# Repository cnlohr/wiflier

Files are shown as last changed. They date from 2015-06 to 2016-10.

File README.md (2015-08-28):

# wiflier, An ESP8266-based Quadcopter Brain

WARNING: This project is still in its early stages!  It doesn't fly yet!

WARNING: Everything surrounding a control loop in control.c for flight IS SUPER JANKEY AND TOTALLY NOT HOW IT SHOULD BE!

WARNING: When I operated the PWM at 3kHz, I had to modify my current board to add pullups on the I2C and short out the AVR's reset to VBat, otherwise it seemed to reboot randomly during flight.

Do you think quadcopters are neat?  Eh, not really for me... BUT I THINK ESP8266's ARE AWESOME!  So, I slapped an LSM9DS1 IMU, a BMP085 barometer and an AVR co-processor with 4 PWM output drivers to a PCB small enough to fit in a hubsan X4 quadcopter.

Picture of the wiflier brain

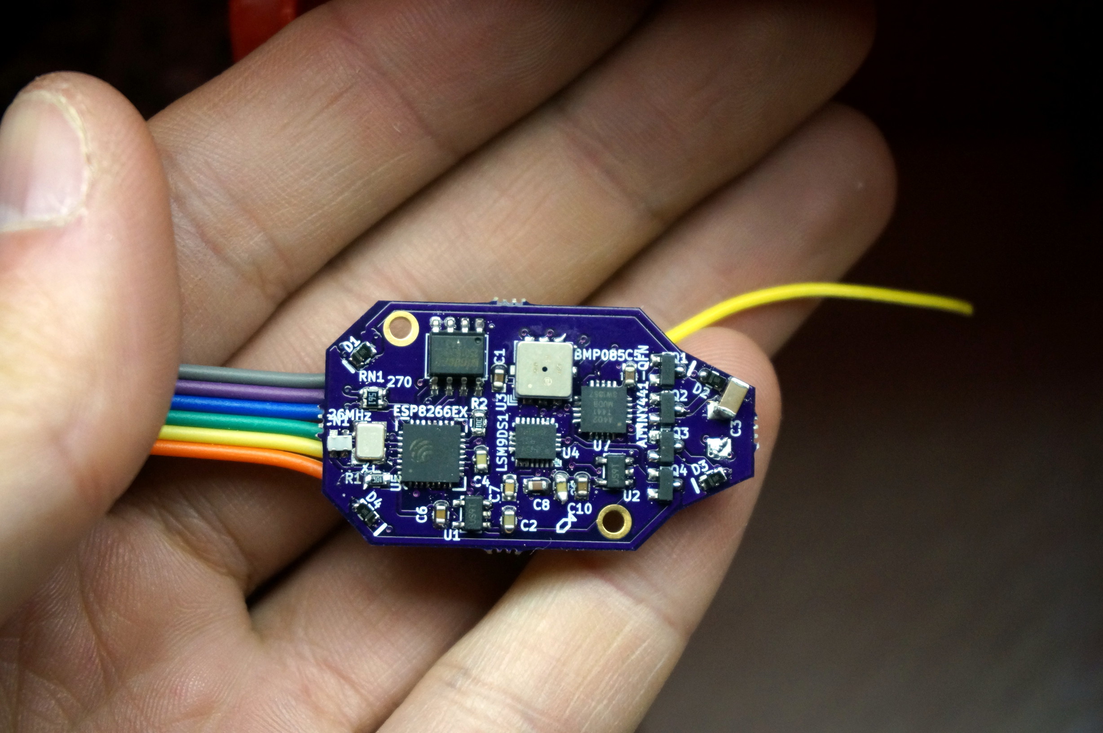
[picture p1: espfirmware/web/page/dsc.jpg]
Picture of Device


Youtube video of the first crack at this:

[!(http://img.youtube.com/vi/3n76iMTHXuE/0.jpg)](http://www.youtube.com/watch?v=3n76iMTHXuE) 

## The Hardware

There is an ESP8266, a 32-bit 80(or 160)MHz processor with 802.11bgn networking at the heart of the system.  This run all the user interface code, and handles all control algorithms.  It is attached to a 2 MByte flash for code and data storage.  It is connected via a software i2c bus to:

* An ATTiny441 with 4 PWM outputs and battery voltage monitoring.
   * 4 6-amp N-channel fets, with diode proection on the AVR's output channels to drive DC motors.
   * Safe-mode, which ramps PWM down after periods of inactivity.
* A LSM9DS1, 9-axis IMU with temperature sensor.  It has a gyro, accelerometer, and magnetometer built in.
* A BMP085, barometer with high precision temperature sensor built in.

## Network connectivity

The wiflier uses an ESP8266, which can act as either a station (mode 1) or a softap (mode 2).  Softap means it broadcasts a SSID that other compuers can connect to.

### Station (Mode 1)

Station mode can be initialized by the ```W1:[ssid]:password``` command.  This will cause the wiflier to connect to the specified network.  It supports WEP, WPA-PSK, and WPA2-PSK.  It will remember this setting when it boots up.  If it fails to connect, it will revert to mode 2.  Currently (maybe?) if it reverts to mode 2, it will stay in mode 2 every subsequent bootup.

If it succeeds in negotiating, it will pull a DHCP lease and print to the serial terminal what that DHCP release is.  All communicat

### Soft AP (Mode 2)

Soft AP mode allows the ESP8266 to create its own wifi network that you can connect to with a wifi-enabled device.  In this mode, one can connect to the new network, and visit the ESP at 192.168.4.1.

This is the default mode.

## Command Interfaces

There are currently two command interfaces to the wiflier.  One is UDP, on port 7777, the other is via HTTP at http://[ip]/d/issue?.

### The UDP interface

For the UDP interface, you can use netcat or 'nc' to communicate with the ESP.  This is partciularly convenient as a command-line tool. You can type

```
nc [ip] 7777 -u
```

To open a terminal to the wiflier.  You can type `T1` and enter.  This should provide a constant stream of telemetry.

When using the UDP interface, you must only have one command per packet.  Packets are the delineation of commands.

### The HTTP interface

If you make an HTTP request to `http://[ip]/d/issue?[command]` where [ip] is the address of the wiflier, and [command] is the command you are issuing, the command will be executed and its return value is sent.  You can check this interface's functionality by going to `http://192.168.4.1/d/issue?T0` and verify it returns a T0 confirmation.  Anything after the question mark will be urldecoded.  Things like amphersands should be URL encoded.

### The websockets interface.

This interface does not yet exist, but I hope to make it a reality.

## Building

This code is separated into two pieces, the ESP firmware and the AVR firmware.

The ESP firmware requires the esp_iot_sdk_v1.1.0, and a copy of the ESP8266 GCC toolchain.  To build the ESP firmware, cd to the espfirmware folder and type 'make'.

The AVR firmware requires avr-libc-1.8.0 and avr-gcc-4.8.1 at a minimum.  To build the AVR firmware, cd to the avr folder, and type 'make'.

## Memory layout:

We use a bit of a modified take on the old memory layout since, while we support OTA upgrades, we do so in a different way than the normal way.

| Address | Size  | Name / Description |
| --- |:-----:| --- |
| 00000h  | 64k | 0x00000.bin, IRAM Code | 
| 10000h  | 180k  | Normally unused, HTTP may be here if signature found.  |
| 3C000h  | 4k | May be used by web interface  |
| 3D000h  | 4k | our device configuration |
| 3E000h  | 8k | May be used by ESP SDK. |
| 40000h  | 240k  | 0x40000.bin, Cached code. |
| 7C000h  | 8k | May be used by ESP SDK. |
| 7E000h  | 8k | May be WiFi configuration |
| 80000h  | 512k  | Scratchpad (Temp only!) |
| 100000h | 1M+ | HTTP data, 1M on W25Q16.  HTTP Used here if signature found. |

## Hardware designs

The wiflier schematics and PCB layout is done in KiCad (2013-07-03).  It should be compatible with newer versions, but is unlikely to be compatible with older versions.  In the hardware/ folder, you'll also find wiflier.lst.  This contains the part identifier, name, digikey part number (if applicable) and cost assuming an order of ~10 boards.

## wiflier UART

The UART on the wiflier is used to send debugging information.  The Wiflier does not currently accept commands via the UART.  I intend to make the UART available to GPS or video input.

## UART flashing the ESP8266.

To UART flash the ESP8266 you will need esptool.py and a serial TTL uart.  USB to serial converters are good. *Do not* use RS-232-level UARTs.  To flash this, you will need to:

1. De-power the device. 
2. Connect GPIO0 to GND.
3. Connect TX, RX and GND (And possibly power) to your UART, reversing TX/RX lines.
4. Apply power to the device.  
5. Then go to the espfirmware folder, and type:

    ```
    ~/esp8266/esptool/esptool.py --port /dev/ttyUSB0 write_flash 0x00000 0x00000.bin 0x40000 0x40000.bin
    ```
    
    or

    ```
    make burn
    ```

6. The esptool should reboot into the running code.

## Net flashing the ESP8266.

Net Flashing the ESP8266 is particularly easy.  Connect to the wiflier, verify you can communicate to it (via HTTP or ping).  Use the 'execute_reflash' tool with the following commands:

```
web/execute_reflash 192.168.4.1 0x00000.bin 0x40000.bin
```

or, from the espfirmware folder...

```
make netburn
```

This will connect to 192.168.4.1, and it will perform the following steps:

1. It will attempt to erase the blocks that need to be written (to 0x00000.bin) using the "FB" command.
  * And await confirmation.
2. It will write the data (0x00000.bin) using the "FW" command.
  * And await confirmation.
3. It will write this first file to 80000h, then it will repeat for the second file, to c0000h.
4. It will then compute the MD5 of the files and execute the "FM" command.
5. Internally, the wiflier will verify the integrety of the written files.
6. At this point, it will disable all interrupts.  Network will go down, etc.
7. It will copy the data from 80000h to 00000h, and then copy c0000h to 40000h.
8. It will then reboot itself and boot into the new code.
9. If a network wasn't found, and it switches to being its own AP... next boot, it should still try to join the old network.

## Flashing the AVR

The AVR is particularly easy to flash.  You'll need:

  * An ISP Programmer, like the TinyISP that operates a 3.3V outputs.
    * Under *NO* condition use a programmer that haves 5V outputs.  This will almost certainly cause severe damage to the wiflier.
  * Associated 6-pin ISP programming connector.
  * AVRDude, or other ISP programming software.
  * A 6-pin male-male connector, SMD preferred.

To flash, follow the following steps:

  1. Connect to a wiflier command interface.
  2. Use the "B0" command to make the ESP8266 release the bus.
    * Failure to do this may damage the AVR or ESP.
  3. Plug the 6-pin male connector into the programming header on the programmer.
  4. Hold the 6-pin connector on the back of the PCB. 
    * Reversing the order will not program, but will not damage the part.
    * You can determine proper order by unplugging power to the quadcopter and flipping the connector around until it powers on.  Powering on indicates proper order.
  5. Initiate programming of the AVR.
	* Failures may indicate the ESP is locking the bus lines.
    * Failures may indicate not all the pins are making contact.
    * Failures may indicate the programming header is reversed.
    * Failures may indicate other problems in the toolchain, i.e. not running programmer as root or having proper credentials.
  6. Remove programmer.
  7. Use the "B1" command to bring the ESP8266 Back online.

## TODO

### Software modifications:

* Try one-shotting the sensors (currently they're in free-run) this will synchronize them to the system clock.
* Try making the system switch over to calling the control loop on interrupt after connection is negotiated, rather than using flags and the idle loop.
* Add WebSockets?
* Add WebGL?
* Separate the control.c into different parts.
* Have some minimal levels of protection for writing to flash, i.e. maybe only allow writing to 0x80000+
* Send some sort of broadcast or discovery packets.
* Figure out why the AVR needs soooo many bytes before it accepts data.

### Hardware modifications:

* Consider making the sensors slaves to the AVR, and having the ESP communicate only to the AVR.
* Consider using the MPL3115A2 instead of the BMP085
* I keep looking at the lack of pullups on the I2C and it makes me nervous when we're running the motor controllers.

## Commands

The heart of the wiflier is the command engine.  This command engine is human-readable, and with the exception of some use cases of the flashing commands is human-readable.

Commands are very simple, they are basically single letters, then parameters, separated by colons.  Responses are usually similar to the command that was sent.  A failure can be indicated by either a lack of response, or an exclaimation point (!) prefixing the response.

As a warning, in some places \r\n is used and in others \n is used.  You should discard \r in all non-binary uses.

### Bn (B1 / B0):  Turn main control loop on/off
Turning the main control loop off will stop all I2C bus communication and resolving what to do in the control loop.  That also means telemetry will stop.

### D
Reboot the system.  This includes the bootloader.  If GPIO0 is held low, the serial bootloader will be initiated.

### Tn (T1 / T0):  Turn streaming of calibrated, filtered telemetry data on/off
This will either continously stream, or turn off streaming of the calibrated telemetry data from the sensors.  Calibration is done using the Rn and Z commands.  Data is tab deliniated.

The streaming format is: ```TD: [frame #]  [GyroX]  [GyroY]  [GyroZ]  [AccX]  [AccY]  [AccZ]  [MagX]  [MagY]  [MagZ]  [Pressure in Bar]  [Temperature in tenths of degrees C]  [battery voltage in 1/100ths of a volt]\n```

### Un (U1 / U0):  Turn streaming of uncalibrated/raw telemtry data on/off
This will enable/disable streaming of uncalibrated telemetry data, straight from the sensors.   Data is tab deliniated.

The streaming format is: ```UD: [frame #]  [GyroX]  [GyroY]  [GyroZ]  [AccX]  [AccY]  [AccZ]  [MagX]  [MagY]  [MagZ]  [Pressure in Bar]  [Temperature in tenths of degrees C]  [battery voltage in 1/100ths of a volt]\n```

For example:
```
UD   9224      600      199      137     2839     1790     2080       61     2214    -4673    101233    368    499 \r\n
UD   9225     -616     -244      304     3208     1797     1934       40     2229    -4673    101233    368    507 \r\n
UD   9226     -687     -234      318     3374     1815     1893       74     2259    -4683    101233    368    507 \r\n
UD   9227      242      240       43     2960     1795     2051       31     2223    -4691    101233    368    507 \r\n
UD   9228      455      146       46     3122     1708     1964       37     2226    -4664    101237    368    507 \r\n
```

### Z: Set 'zero'
Sending a Z will set the zero all gyros, and accelerometer X and accelerometer Y.  This will only have an effect on the calibrated, filtered telemetry data.

### Rn (R1 / R0): Enable range calibration.
When you want to begin range calibration (for accelerometer Z, and all mag inputs) send R1.  This will begin to look for peak positive and negative values.  When you execute R0, it will take whatever the maximums are and scale all data to that range.

### P: Print calibration and other system data.
When you send a 'P' command, the wiflier will send back all calibration and possibly other system data.  As of the time of writing this the following values are returned:

```
    P6
    #GC\t x \t y \t z (Gyro Zero)
    #AC\t x \t y \t z (Accelerometer Zero)
    #AL\t x \t y \t z (Accelerometer Minimum)
    #AM\t x \t y \t z (Accelerometer Maximum)
    #ML\t x \t y \t z (Magnetometer Minimum)
    #MH\t x \t y \t z (Magnetometer Maximum)
```

### S: Save calibration and other settings.
This writes the current information in the global `settings` value to the flash at address 3D000h.

### Mx: Motor control functions

#### M?: Motor query

Returns if motors are in automatic mode (1/0) and all motor speeds, 0..255 speed.

`M?` will return `M?[automatic]:[M0 speed]:[M1 speed]:[M2 speed]:[M3 speed]\r\n"

#### MA: Motors in automatic mode

Selecting this function will move the move the motors into automatic mode, allowing a control algorithm to take them over.

(Not currently implemented)

#### MM: Motors in manual mode

Disable automatic control of motors, they will now respond to the M(number) commands.  Optionally, can take up to 4 arguments for the new motor set values.

#### M0, M1, M2, M3: Set motor speed.

If you want to control an individual motor speed, you call `Mn:speed` for example `M0:127` would turn motor 0 on to half duty cycle.  This only works if the motors are in manual mode.

### Fx: Flash commands

#### FEn: Flash Erase Sector

Erase a specific flash sector, it will erase the flash starting at address n*4096 to n*4096+4095.  This function works with flash memory below and above the 1MB barrier, however it takes a moment to execute and no interrupts may run while it is executing.

#### FBn: Flash Erase Block

Erase a specific block of flash.  This operates on a whole 64kB block, and takes about as long as it takes FE to erase just one sector.  This function does not work past the 1MB barrier.

#### FW: Flash Write

This function writes flash. It requires two parameters, the first is the starting addres, the second is the size (in bytes).   Writes must be aligned to 4-byte boundaries, sizes must line to 4-byte boundaries.

```
    FW40:8:hello\r\n
```

Will write `hello\r\n\0` to memory address 40 (which will break booting, so don't do this), and it will respond with:

```
    FW40
```

#### FR: Flash Read

This will read back from the flash, starting at the first parameter and with length of the second.

```
    FR40:8\r\n
```

Will read from address 40 8 bytes and if we've executed the terrible terrible example above, respond with:

```
    FR00000040:0008:hello\r\n\0
```

#### FM: Rewrite boot flash

This function takes several parameters, in the style: ```FMa:b:c:d:e:f:g:h``` where 

   1. A = Address to copy from #1
   2. B = Address to copy to #1  (Must be 65kB aligned)
   3. C = Number of bytes to copy #1 (Must be 1k chunks)
   4. D = MD5 of entire 'from #1' range.
   5. E = Address to copy from #2
   6. F = Address to copy to #2  (Must be 65kB aligned)
   7. G = Number of bytes to copy #2 (Must be 1k chunks)
   8. H = MD5 of entire 'from #2' range.

This will verify both MD5's before copying.  Interrupts will continue to execute until the actual flash-over begins.  Once flash-over is complete, the device will automatically reboot.

An example would be:

```
FM524288:0:33792:d6f04e459bc9aefabd9ed80981e6837f:786432:262144:171008:8435d1904110eacb66771320f63736bc
```

It should respond with ```FM``` In the event of a failure, it will also send a ```!FM[code]```.

### Wx: Wireless/Network commands.

#### W1: Connect to wifi network.

If you want to connect to an existing wifi network, you can use the W1 command.  This will find the specified AP, and join.  An example W1 command would be ```W1:ssid:password```.  This will connect to network with name 'ssid', and password 'password'.  If it fails to connect, it will switch back to softap mode.

#### W2: Make softAP network

This will cause the ESP8266 to make its own network. You can connect to it.  Its IP will be 192.168.4.1

#### WI: Get current settings

This will cause the ESP8266 to give you the mode (1 or 2) SSID, and password of the current network status.

For example ```WI``` will return ```WI1:mynetwork:mypassword```.

#### WS: Scan for networks

**WARNING**: If operating in mode 2, this will cause the ESP to go offline momentarily while it scans!

If you issue the ```WS``` command, the ESP8266 will begin a scan. It is unlikely to return any response at all. You can read the returned networks with the ```WR``` command.

It may take several seconds for the WS command to complete.

#### WR: Return wireless networks from last scan.

After you scan for networks, you can probe for responses to those networks with the ```WR``` command.  It returns ```WRn``` where n is the number of networks found.  It will then provide the networks in a tab delinated data format as follows:

```
#SSID MAC RSSI Channel Encryption
```

For example a response to the ```WR``` command could be:

```
WR3
#quiddles       00:23:15:11:22:41       -44     1       open
#reads          08:18:a0:02:4d:cc       -55     1       wpa2
#rguest         0a:14:c1:f3:02:a0       -68     11      open
```

### J: Joystick commands

***SECTION NOT WRITTEN***

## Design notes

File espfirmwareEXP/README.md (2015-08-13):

#ESP8266 I2S WS2812 Driver 

(For more reliable WS2812 driving...)

This project is based off of the I2S interface for the mp3 player found here:
https://github.com/espressif/esp8266_mp3_decoder/

If you want more information about the build environment, etc.  You should 
check out the regular WS2812 driver, found here: https://github.com/cnlohr/ws2812esp8266

This project is still jankey and needs some cleanup.  The way it currently works is to
continuously send WS2812 frames and when new data comes in on port 7777, it just updates the frames.

I wanted to make it so it would stop doing all DMA proesses so it could save bus contention, but I couldn't figure out how to make that happen.  If I tried disabling and re-enabling, it seems to have caused the DMA to just freak out and turn off until chip reboot.

The WS2812 output is synthesized from the input buffer.   Any time a 0 is to be transmitted, we need a .3us pulse high and .9us low.  If a 1, then we send a .9us high with a .3us low.  The way we do this is we look at nibbles, i.e.:

0101 would convert into:
1000 1110 1000 1110 < bitstream that actually gets shipped out.

Unfortunately this does mean it takes up 4x the space in RAM to DMA the data... But, it is very fast and efficient.

## Hardware Connection

Unfortunately the I2S Output pin is the same as RX1 (pin 25), which means if you are programming via the UART, it'll need to be unplugged any time you're testing.  The positive side of this is that it is a pin that is exposed on most ESP8266 breakout boards.

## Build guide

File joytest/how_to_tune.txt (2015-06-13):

THIS DOES NOT WORK!!!

To tune L/R: Set tuning to:
N0:0:0:12600:####:0:0:12600:0:0:0:12600

#### = High P value (400 worked for me)

Try running the craft.

Get an oscillation.

Open oscillation in OpenOffice.

Find period of oscillation (from 0 to high, to 0 to low to 0)

I.e. rows 2659 to 2724... 65

Zeigler Nichols says: Ku = 120, Tu = 65
 Kp = .6Ku     Kp = 72
 Ki = 2Kp/Tu   Ki = 3
 Kd = Kp*Tu/8  Kd = 585

N0:0:0:12600:72:3:585:12600:0:0:0:12600
Err try this:
NP1000:100:0:12600:16000:200:0:12600:16000:200:0:12600

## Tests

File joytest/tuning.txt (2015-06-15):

NP0:100:0:12600:2000:50:0:12600:2000:50:0:12600

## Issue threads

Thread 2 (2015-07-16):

How have you made the PCB?

Pablotis, 2015-07-16:
I suppose you have designed the PCB but, have you soldered it or have ordered it? Because it seems to be made from a machine, could you give me the link please?
A lot of thanks!!
I love your proyect!!

cnlohr, 2015-07-16:
Well, I used oshpark for the board and populated it myself.  BUT! I will be branching off in the next 2 weeks to a brand new version.  I can give you links to the old one if you want, BUT! The new one is coming soon, and once I'm sure I'm happy with the hardware, I might be getting them made professionally.

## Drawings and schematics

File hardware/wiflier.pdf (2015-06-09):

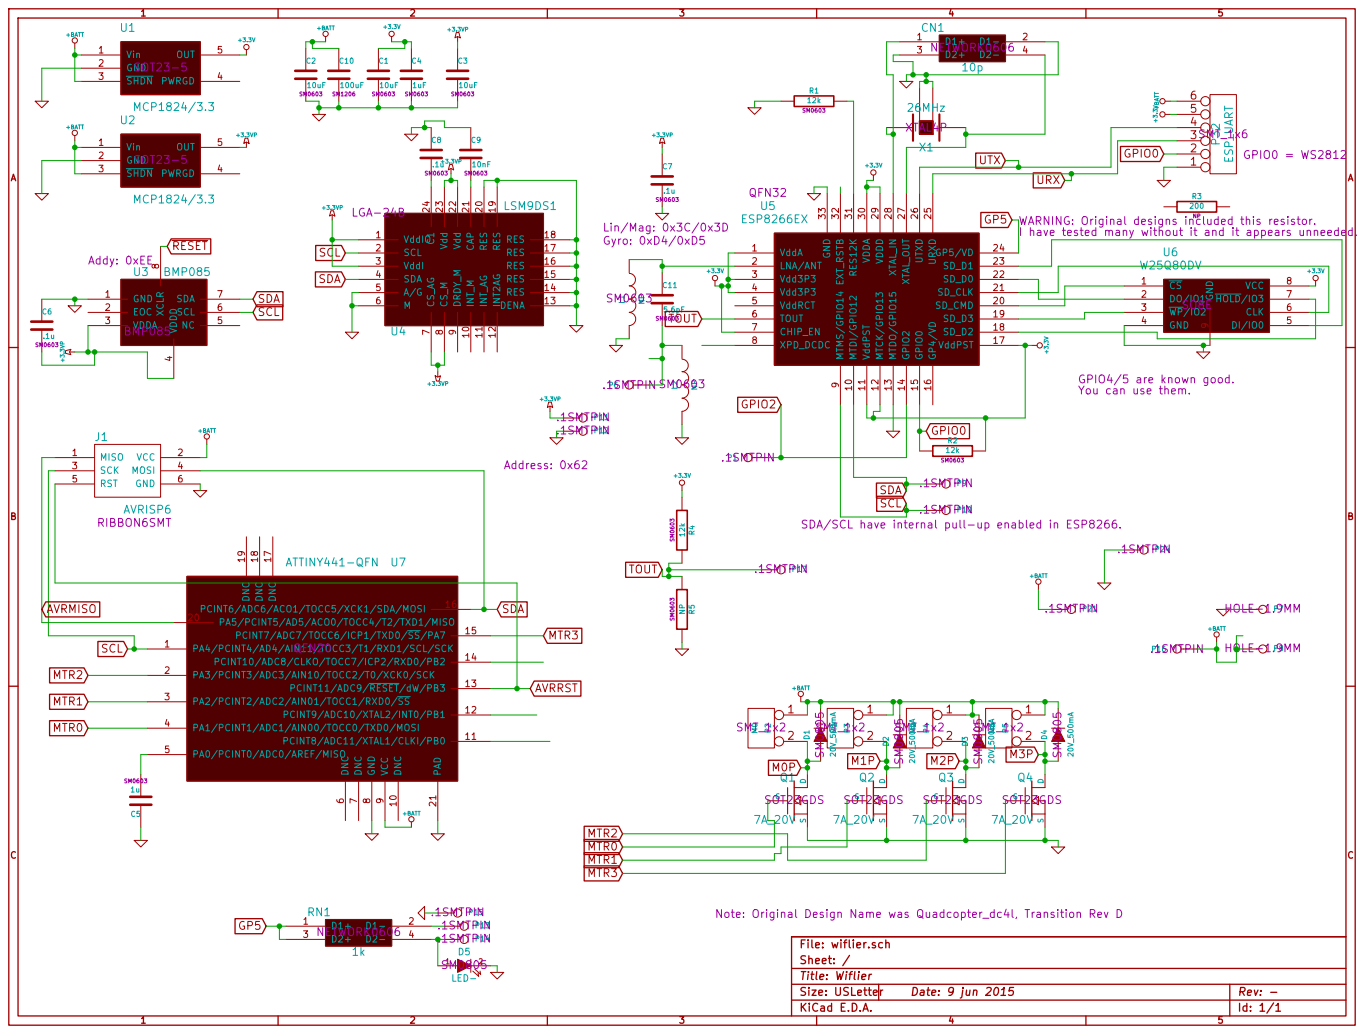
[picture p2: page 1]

I have tested many without it and it appears unneeded. R1

9 INT_M 10 RES 20 INT_AG 11 CAP 21 INT2AG 12 Vdd 22 DENA 13 Vdd 23 RES 14 C1 24 RES 15 RES 16 RES 17 RES 18 RES 19 U4

9 MTDI/GPIO12 10 SD_CMD 20 VDDA 30 VddPST 11 SD_CLK 21 RES12K 31 MTCK/GPIO13 12 SD_D0 22 EXT_RSTB 32 MTDO/GPIO15 13 SD_D1 23 GND 33 GPIO2 14 GP5/VD 24 GPIO0 15 URXD 25 GP4/VD 16 UTXD 26 VddPST 17 XTAL_OUT 27 SD_D2 18 XTAL_IN 28 SD_D3 19 VDDD 29U5 ESP8266EX

4 NC 5 SCL 6 SDA 7 XCLR

9 DNC 10 PA5/PCINT5/AD5/ACO0/TOCC4/T2/TXD1/MISO 20 PCINT8/ADC11/XTAL1/CLKI/PB0 11 PAD 21 PCINT9/ADC10/XTAL2/INT0/PB1 12 PCINT11/ADC9/RESET/dW/PB3 13 PCINT10/ADC8/CLKO/TOCC7/ICP2/RXD0/PB2 14 PCINT7/ADC7/TOCC6/ICP1/TXD0/SS/PA7 15 PCINT6/ADC6/ACO1/TOCC5/XCK1/SDA/MOSI 16 DNC 17 DNC 18 DNC 19 ATTINY441-QFN U7 QFN20 MISO 1 VCC 2 SCK 3 MOSI 4 RST 5 GND 6 J1 AVRISP6

Note: Original Design Name was Quadcopter_dc4l, Transition Rev D

Id: 1/1 Title: Wiflier File: wiflier.sch Sheet: /

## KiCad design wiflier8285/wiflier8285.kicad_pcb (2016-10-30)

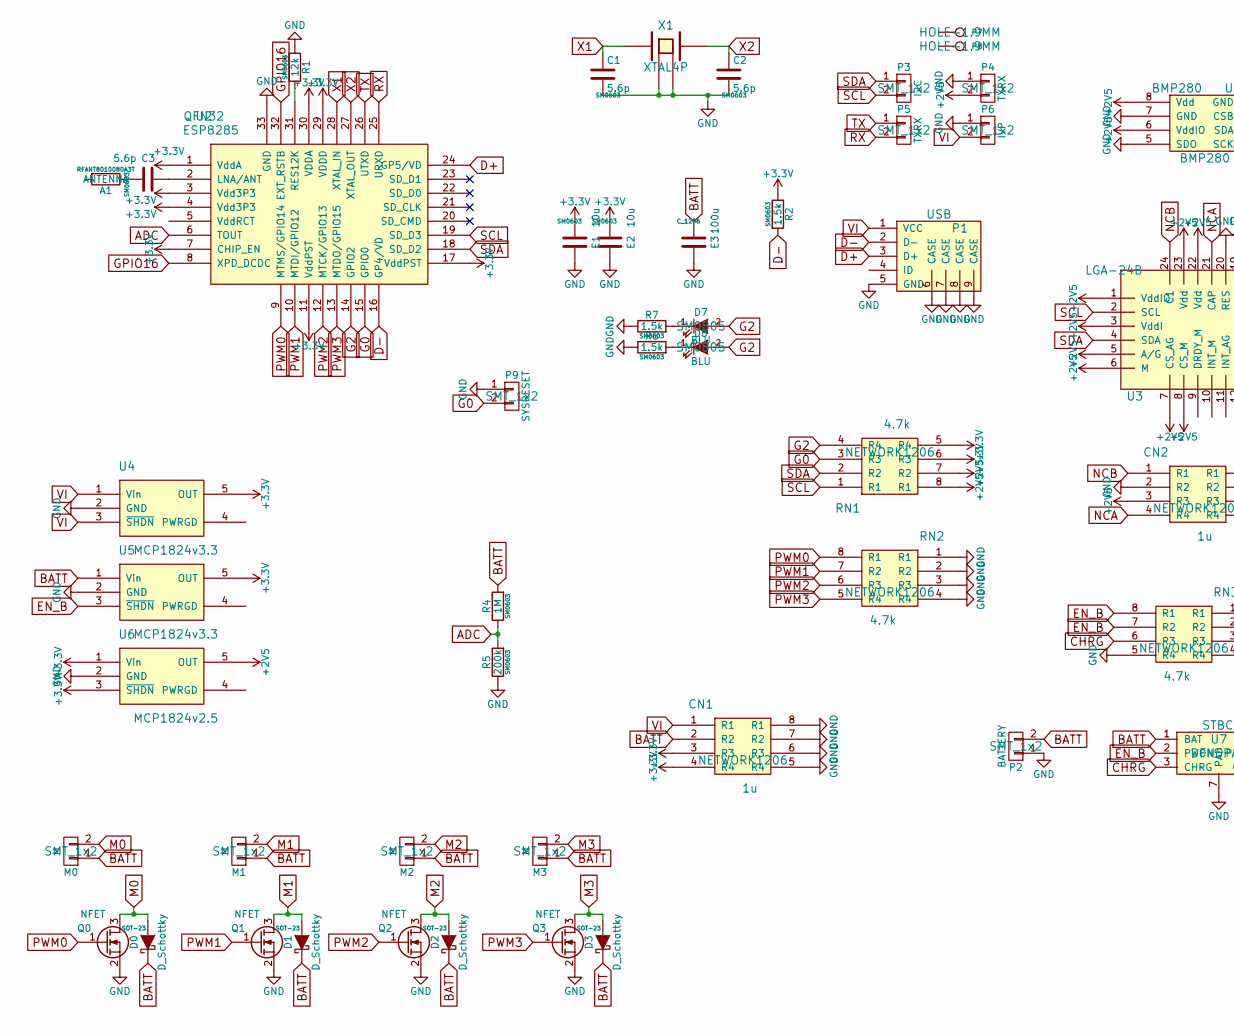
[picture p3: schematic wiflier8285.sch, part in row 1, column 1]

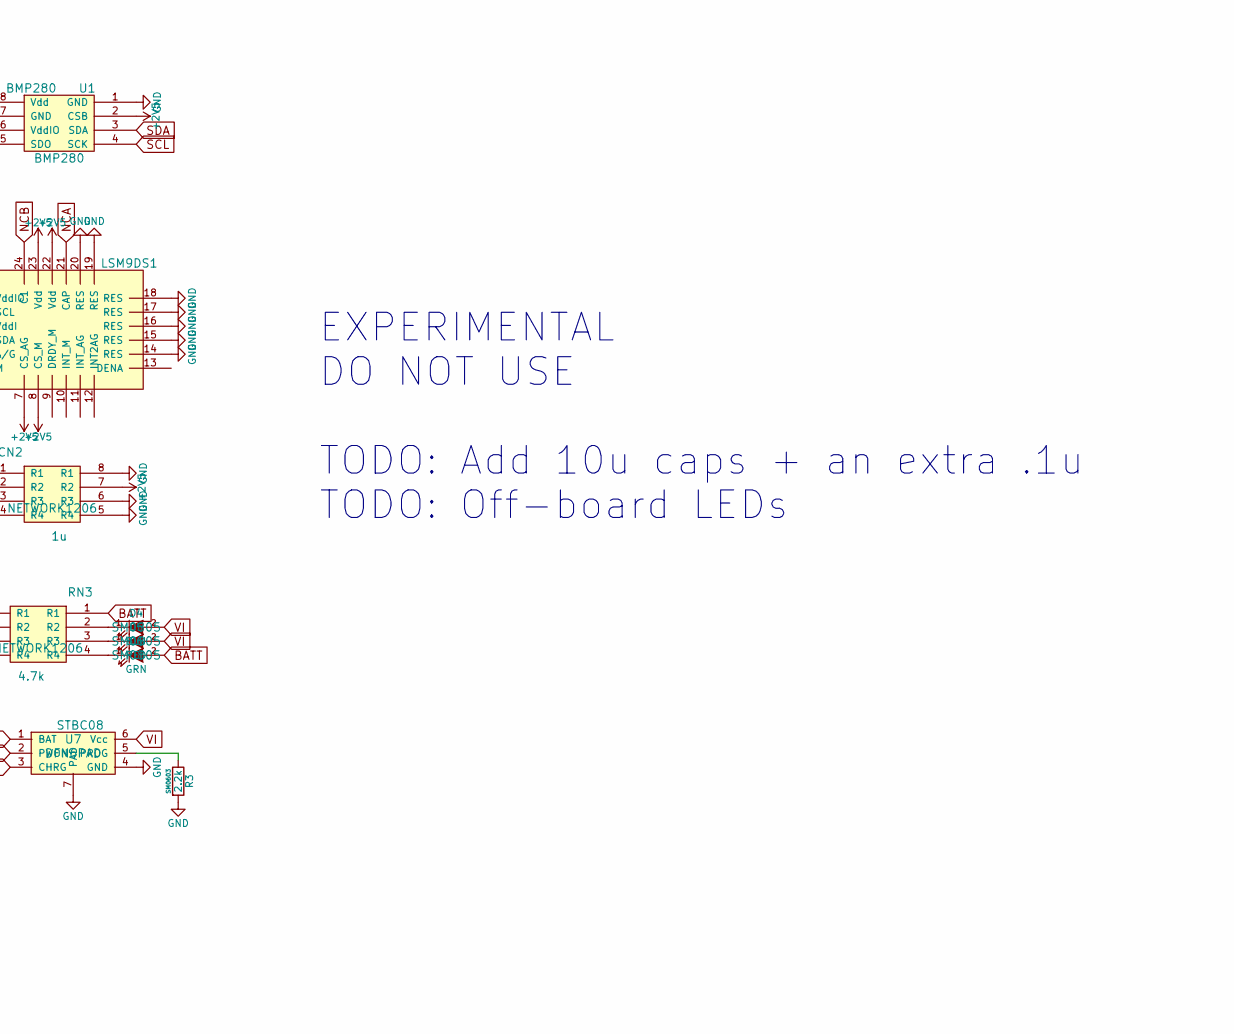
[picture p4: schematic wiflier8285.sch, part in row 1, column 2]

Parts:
A1: ANTENNA; RFANT8010080A3T
C1, C2, C3: 5.6p; SM0603
CN1, CN2: 1u; NETWORK1206
D0, D1, D2, D3: D_Schottky; SMini2-F5-B; Digikey DB2J41100LCT-ND
D4, D7, D8: BLU; SM0805
D5: RED; SM0805
D6: GRN; SM0805
E1, E2: 10u; SM0603
E3: 100u; C_1206
M0, M1, M2, M3: M; SMT_1x2
P1: USB; USBMicroB-10118194-0001LF
P2: BATTERY; SMT_1x2
P3: I2C; SMT_1x2
P4, P5: TXRX; SMT_1x2
P6: IVP; SMT_1x2
P7, P8: M; HOLE-1.9MM
P9: SYSRESET; SMT_1x2
Q0, Q1, Q2, Q3: NFET; SOT-23; Digikey IRLML6244TRPBFCT-ND
R1: 12k; SM0603
R2, R6, R7: 1.5k; SM0603
R3: 2.2k; SM0603
R4: 1M; SM0603
R5: 200k; SM0603
RN1, RN2, RN3: 4.7k; NETWORK1206
U1: BMP280
U2: ESP8285; QFN32
U3: LSM9DS1; LGA-24B
U4, U5: MCP1824v3.3; SOT-23-5
U6: MCP1824v2.5; SOT-23-5
U7: STBC08; DFN6PAD
X1: XTAL4P; XTAL4TINY

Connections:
+2V5: CN2.3 (R3), CN2.7 (R2), P4.2, RN1.7 (R2), RN1.8 (R1), U1.2 (CSB), U1.6 (VddIO), U1.8 (Vdd), U3.1 (VddIO), U3.3 (VddI), U3.5 (A/G), U3.6 (M), U3.7 (CS_AG), U3.8 (CS_M), U3.22 (Vdd), U3.23 (Vdd), U6.5 (OUT)
+3V3: CN1.3 (R3), CN1.4 (R4), E1.2, E2.2, R2.1, RN1.5 (R4), RN1.6 (R3), U2.1 (VddA), U2.3 (Vdd3P3), U2.4 (Vdd3P3), U2.7 (CHIP_EN), U2.11 (VddPST), U2.17 (VddPST), U2.29 (VDDD), U2.30 (VDDA), U4.5 (OUT), U5.5 (OUT), U6.1 (Vin), U6.3 (~SHDN)
ADC: R4.1, R5.2, U2.6 (TOUT)
BATT: CN1.2 (R2), D0.1 (K), D1.1 (K), D2.1 (K), D3.1 (K), D6.2 (A), E3.2, M0.1, M1.1, M2.1, M3.1, P2.2, R4.2, RN3.1 (R1), U5.1 (Vin), U7.1 (BAT)
CHRG: RN3.6 (R3), U7.3 (CHRG)
D+: P1.3 (D+), U2.24 (GP5/VD)
D-: P1.2 (D-), R2.2, U2.16 (GP4/VD)
EN_B: RN3.7 (R2), RN3.8 (R1), U5.3 (~SHDN), U7.2 (PWON)
G0: P9.2, RN1.3 (R3), U2.15 (GPIO0)
G2: D7.2 (A), D8.2 (A), RN1.4 (R4), U2.14 (GPIO2)
GND: C1.2, C2.2, CN1.5 (R4), CN1.6 (R3), CN1.7 (R2), CN1.8 (R1), CN2.2 (R2), CN2.5 (R4), CN2.6 (R3), CN2.8 (R1), E1.1, E2.1, E3.1, P1.5 (GND), P1.6 (CASE), P1.7 (CASE), P1.8 (CASE), P1.9 (CASE), P2.1, P4.1, P6.1, P9.1, Q0.2 (S), Q1.2 (S), Q2.2 (S), Q3.2 (S), R1.1, R3.2, R5.1, R6.1, R7.1, RN2.1 (R1), RN2.2 (R2), RN2.3 (R3), RN2.4 (R4), RN3.5 (R4), U1.1 (GND), U1.5 (SDO), U1.7 (GND), U2.33 (GND), U3.14 (RES), U3.15 (RES), U3.16 (RES), U3.17 (RES), U3.18 (RES), U3.19 (RES), U3.20 (RES), U4.2 (GND), U5.2 (GND), U6.2 (GND), U7.4 (GND), U7.7 (PAD), X1.3 (GND), X1.4 (GND)
GPIO16: U2.8 (XPD_DCDC), U2.32 (EXT_RSTB)
M0: D0.2 (A), M0.2, Q0.3 (D)
M1: D1.2 (A), M1.2, Q1.3 (D)
M2: D2.2 (A), M2.2, Q2.3 (D)
M3: D3.2 (A), M3.2, Q3.3 (D)
NCA: CN2.4 (R4), U3.21 (CAP)
NCB: CN2.1 (R1), U3.24 (C1)
unnamed: A1.1, C3.2
unnamed: C3.1, U2.2 (LNA/ANT)
unnamed: D4.1 (K), RN3.2 (R2)
unnamed: D5.1 (K), RN3.3 (R3)
unnamed: D6.1 (K), RN3.4 (R4)
unnamed: D7.1 (K), R7.2
unnamed: D8.1 (K), R6.2
unnamed: R1.2, U2.31 (RES12K)
unnamed: R3.1, U7.5 (PROG)
PWM0: Q0.1 (G), RN2.8 (R1), U2.9 (MTMS/GPIO14)
PWM1: Q1.1 (G), RN2.7 (R2), U2.10 (MTDI/GPIO12)
PWM2: Q2.1 (G), RN2.6 (R3), U2.12 (MTCK/GPIO13)
PWM3: Q3.1 (G), RN2.5 (R4), U2.13 (MTDO/GPIO15)
RX: P5.2, U2.25 (URXD)
SCL: P3.2, RN1.1 (R1), U1.4 (SCK), U2.19 (SD_D3), U3.2 (SCL)
SDA: P3.1, RN1.2 (R2), U1.3 (SDA), U2.18 (SD_D2), U3.4 (SDA)
TX: P5.1, U2.26 (UTXD)
VI: CN1.1 (R1), D4.2 (A), D5.2 (A), P1.1 (VCC), P6.2, U4.1 (Vin), U4.3 (~SHDN), U7.6 (Vcc)
X1: C1.1, U2.28 (XTAL_IN), X1.1
X2: C2.1, U2.27 (XTAL_OUT), X1.2

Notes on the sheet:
EXPERIMENTAL DO NOT USE TODO: Add 10u caps + an extra .1u TODO: Off-board LEDs

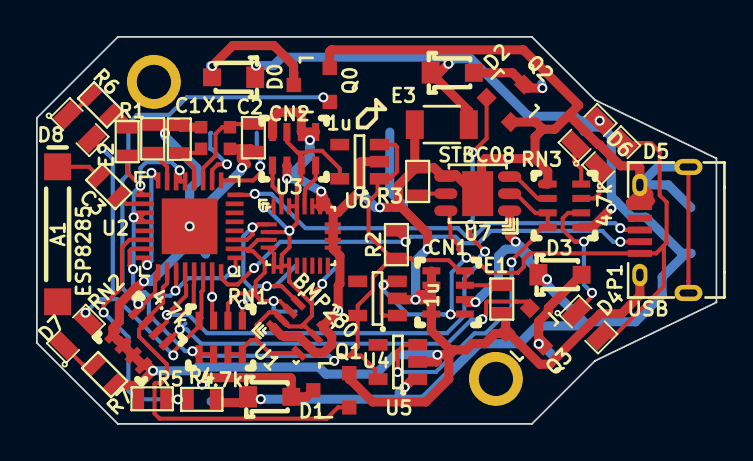
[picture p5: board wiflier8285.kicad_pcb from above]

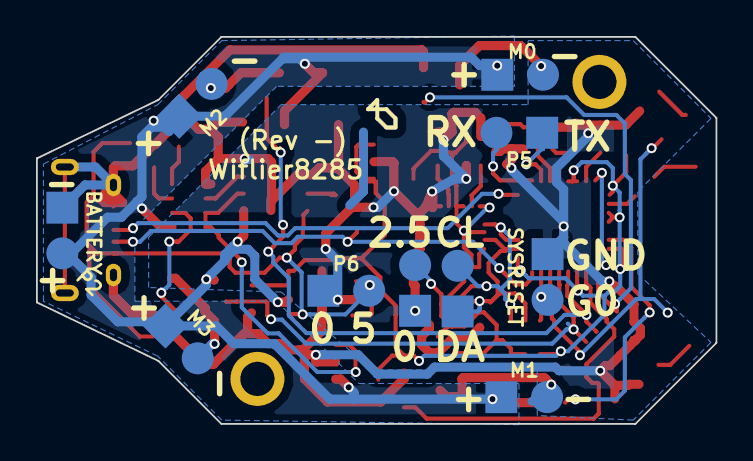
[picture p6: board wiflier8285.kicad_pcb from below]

Board: 2 copper layers, 37.8 x 21.5 mm, 53 parts (10 on the bottom side), 38 nets.

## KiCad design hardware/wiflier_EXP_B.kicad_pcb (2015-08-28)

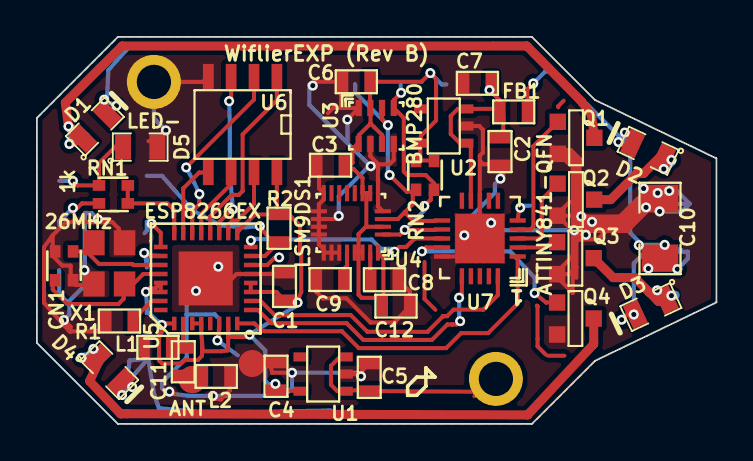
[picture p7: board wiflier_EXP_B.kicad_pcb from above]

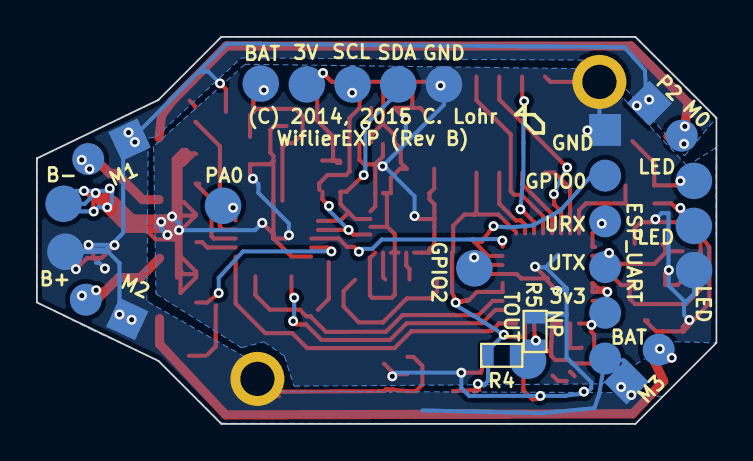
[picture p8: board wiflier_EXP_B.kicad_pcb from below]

Board: 2 copper layers, 37.8 x 21.5 mm, 61 parts (20 on the bottom side), 41 nets.

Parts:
C1, C2, C3, C5: 10uF; SM0603
C4: 1uF; SM0603
C6, C8, C12: .1u; SM0603
C7: .1uF; SM0603
C9: 10nF; SM0603
C10: 100uF; SM1206
C11: 5.6pF; SM0603
CN1: 10p; NETWORK0606
D1, D2, D3, D4: 20V_500mA; SM0805
D5: LED-; SM0805
FB1: -; SM0603
L1, L2: NP; SM0603
P1: GPIO2; .1SMTPIN
P2: M0; SMT_1x2
P3: M1; SMT_1x2
P4: M2; SMT_1x2
P5: M3; SMT_1x2
P6, P19: ANT; .1SMTPIN
P7, P8: HOLE-1.9MM
P9: SDA; .1SMTPIN
P10: SCL; .1SMTPIN
P11: 3V; .1SMTPIN
P12: GND; .1SMTPIN
P13, P14, P15: LED; .1SMTPIN
P16: BAT; .1SMTPIN
P17: TOUT; .1SMTPIN
P18: PA0; .1SMTPIN
P21: B+; .1SMTPIN
P24: B-; .1SMTPIN
P32: ESP_UART; SMT_1x6
Q1, Q2, Q3, Q4: 7A_20V; SOT23GDS
R1, R2, R4: 12k; SM0603
R5: NP; SM0603
RN1, RN2: 1k; NETWORK0606
U1: MCP1824/3.3; SOT23-5
U2: MCP1824/3.0; SOT23-5
U3: BMP280
U4: LSM9DS1; LGA-24B
U5: ESP8266EX; QFN32
U6: W25Q16DV; SO8E
U7: ATTINY841-QFN; QFN20
X1: 26MHz; XTAL4P

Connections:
+3.3V: C1.1, C4.1, P32.5, R2.2, R4.1, U1.5, U5.1, U5.3, U5.4, U5.7, U5.11, U5.12, U5.17, U5.29, U5.30, U6.8
+3.3VP: C3.1, C6.1, C12.1, P11.1, RN2.2, RN2.4, U2.5, U3.2, U3.6, U3.8, U4.1, U4.3, U4.7, U4.8, U4.22, U4.23
+BATT: C5.1, C10.1, D1.2, D2.2, D3.2, D4.2, FB1.2, P2.1, P3.1, P4.1, P5.1, P8.1, P21.1, P32.6, U1.1, U1.3
AVRMISO: U5.10, U7.20
AVRMOSI: U5.9, U7.16
AVRRST: U5.16, U7.13
AVRSCK: U5.8, U7.1
GND: C1.2, C2.2, C3.2, C4.2, C5.2, C6.2, C7.2, C8.1, C9.1, C10.2, C12.2, CN1.2, CN1.3, D5.2, L1.2, L2.2, P7.1, P12.1, P15.1, P19.1, P24.1, P32.1, Q1.S, Q2.S, Q3.S, Q4.S, R1.1, R5.2, U1.2, U2.2, U3.1, U3.5, U3.7, U4.5, U4.6, U4.13, U4.14, U4.15, U4.16, U4.17, U4.18, U4.19, U4.20, U5.13, U5.33, U6.4, U7.8, U7.15, U7.21, X1.3, X1.4
GP5: RN1.1, RN1.3, U5.24
GPIO0: P32.2, R2.1, U5.15
GPIO2: P1.1, U5.14
M0P: D1.1, P2.2, Q1.D
M1P: D2.1, P3.2, Q2.D
M2P: D3.1, P4.2, Q3.D
M3P: D4.1, P5.2, Q4.D
MTR0: Q1.G, U7.4
MTR1: Q2.G, U7.3
MTR2: Q3.G, U7.2
MTR3: Q4.G, U7.14
unnamed: P18.1, U7.5
unnamed: P13.1, RN1.2
unnamed: C8.2, U4.24
unnamed: C9.2, U4.21
unnamed: C11.1, L1.1, U5.2
unnamed: C11.2, L2.1, P6.1
unnamed: D5.1, P14.1, RN1.4
unnamed: R1.2, U5.31
unnamed: U5.20, U6.1
unnamed: U5.21, U6.6
unnamed: U5.22, U6.2
unnamed: U5.23, U6.5
unnamed: CN1.1, U5.28, X1.2
unnamed: U5.19, U6.3
unnamed: U5.18, U6.7
unnamed: CN1.4, U5.27, X1.1
SCL: P10.1, RN2.3, U3.4, U4.2, U7.12
SDA: P9.1, RN2.1, U3.3, U4.4, U7.11
TOUT: P17.1, R4.2, R5.1, U5.6
URX: P32.3, U5.25
UTX: P32.4, U5.26
VAA: C2.1, C7.1, FB1.1, P16.1, U2.1, U2.3, U7.9

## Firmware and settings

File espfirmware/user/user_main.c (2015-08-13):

#include "mem.h"
#include "c_types.h"
#include "user_interface.h"
#include "ets_sys.h"
#include "driver/uart.h"
#include "osapi.h"
#include "espconn.h"
#include "i2c.h"
#include "control.h"
#include "mystuff.h"
#include "ip_addr.h"
#include "http.h"
#include "spi_flash.h"
#include "esp8266_rom.h"

#define MAX_FRAME 2000

#define procTaskPrio        0
#define procTaskQueueLen    1

static volatile os_timer_t some_timer;
static struct espconn *pUdpServer;
static struct espconn *pHTTPServer;



//Tasks that happen all the time.

int jr;
os_event_t    procTaskQueue[procTaskQueueLen];

volatile int tick_flag = 0;

static void ICACHE_FLASH_ATTR
procTask(os_event_t *events)
{
	static int printed_ip;
	system_os_post(procTaskPrio, 0, 0 );
	jr++;

	HTTPTick(0);

	//TRICKY! If we use the timer to initiate this, connecting to people's networks
	//won't work!  I don't know why, so I do it here.  this does mean sometimes it'll
	//pause, though.
	if( tick_flag )
	{
		tick_flag = 0;
		controltimer( );
		HTTPTick(1);
	}

	if( events->sig == 0 && events->par == 0 )
	{
		//Idle Event.
		struct station_config wcfg;
		char stret[256];
		char *stt = &stret[0];
		struct ip_info ipi;

		int stat = wifi_station_get_connect_status();

//		printf( "STAT: %d\n", stat );

		if( stat == STATION_WRONG_PASSWORD || stat == STATION_NO_AP_FOUND || stat == STATION_CONNECT_FAIL )
		{
			wifi_set_opmode_current( 2 );
			stt += ets_sprintf( stt, "Connection failed: %d\n", stat );
			uart0_sendStr(stret);
		}

		if( stat == STATION_GOT_IP && !printed_ip )
		{
			wifi_station_get_config( &wcfg );
			wifi_get_ip_info(0, &ipi);
			stt += ets_sprintf( stt, "STAT: %d\n", stat );
			stt += ets_sprintf( stt, "IP: %d.%d.%d.%d\n", (ipi.ip.addr>>0)&0xff,(ipi.ip.addr>>8)&0xff,(ipi.ip.addr>>16)&0xff,(ipi.ip.addr>>24)&0xff );
			stt += ets_sprintf( stt, "NM: %d.%d.%d.%d\n", (ipi.netmask.addr>>0)&0xff,(ipi.netmask.addr>>8)&0xff,(ipi.netmask.addr>>16)&0xff,(ipi.netmask.addr>>24)&0xff );
			stt += ets_sprintf( stt, "GW: %d.%d.%d.%d\n", (ipi.gw.addr>>0)&0xff,(ipi.gw.addr>>8)&0xff,(ipi.gw.addr>>16)&0xff,(ipi.gw.addr>>24)&0xff );
			stt += ets_sprintf( stt, "WCFG: /%s/%s/\n", wcfg.ssid, wcfg.password );
			uart0_sendStr(stret);
			printed_ip = 1;
		}
	}
}




void ICACHE_FLASH_ATTR at_recvTask()
{
	//Called from UART.	
}

void ICACHE_FLASH_ATTR MyTimer(void *arg)
{
	tick_flag = 1;
}

void user_rf_pre_init(void)
{
	//nothing.
}

char * strcat( char * dest, char * src )
{
	return strcat(dest, src );
}

void ICACHE_FLASH_ATTR user_init(void)
{
	int i;
restart:

	uart_init(BIT_RATE_115200, BIT_RATE_115200);

 	gpio_init();

	//Remap MTD to GPIO
	PIN_FUNC_SELECT(PERIPHS_IO_MUX_MTDI_U, FUNC_GPIO12); 
	PIN_FUNC_SELECT(PERIPHS_IO_MUX_MTMS_U, FUNC_GPIO14); 

	//~60k resistor.  On a small PCB, with 3 I2C clients, it takes ~ 1uS to get to 2v
	PIN_PULLUP_EN(PERIPHS_IO_MUX_MTDI_U);
	PIN_PULLUP_EN(PERIPHS_IO_MUX_MTMS_U); 

	gpio_output_set( 0x00000000, 0x00000000, 0x00000000, 0xffffffff );

	ConfigI2C();

	ControlInit(); //Reads out configuration.

	int wifiMode = wifi_get_opmode();
	printf( "Wifi Mode: %d (", wifiMode );
	if( wifiMode == SOFTAP_MODE )
	{
		struct softap_config c;
		wifi_softap_get_config( &c );

		printf( "SoftAP)\n SSID: %s\n PASS: %s\n Channel: %d\n Auth Mode: %s\n", c.ssid, c.password, c.channel, enctypes[c.authmode] );
	}
	else if( wifiMode == STATION_MODE )
	{
		struct station_config c;
		wifi_station_get_config( &c );
		wifi_station_dhcpc_start();
		printf( "Station)\n SSID: %s\n PASS: %s\n BSSID SET: %d\n", c.ssid, c.password, c.bssid_set );
	}
	else
	{
		printf( "%d)\n", wifiMode );
	}

//Nope! Read configuration from flash.
//	wifi_set_opmode( 2 ); //We broadcast our ESSID, wait for peopel to join.

    pUdpServer = (struct espconn *)os_zalloc(sizeof(struct espconn));
	ets_memset( pUdpServer, 0, sizeof( struct espconn ) );
	pUdpServer->type = ESPCONN_UDP;
	pUdpServer->proto.udp = (esp_udp *)os_zalloc(sizeof(esp_udp));
	pUdpServer->proto.udp->local_port = 7777;
	espconn_regist_recvcb(pUdpServer, issue_command);

	if( espconn_create( pUdpServer ) )
	{
		uart0_sendStr( "UDP FAULT\r\n" );
		goto restart;
	}

	pHTTPServer = (struct espconn *)os_zalloc(sizeof(struct espconn));
	ets_memset( pHTTPServer, 0, sizeof( struct espconn ) );
	espconn_create( pHTTPServer );
	pHTTPServer->type = ESPCONN_TCP;
    pHTTPServer->state = ESPCONN_NONE;
	pHTTPServer->proto.tcp = (esp_tcp *)os_zalloc(sizeof(esp_tcp));
	pHTTPServer->proto.tcp->local_port = 80;
    espconn_regist_connectcb(pHTTPServer, httpserver_connectcb);
    espconn_accept(pHTTPServer);
    espconn_regist_time(pHTTPServer, 15, 0); //timeout


	ets_wdt_disable();

	int i2ctries = 0;
printf( "Starting I2C\n" );
retryi2c:
	ConfigI2C();

	if( i2ctries++ > 10 )
	{
		goto skip_i2c;
	}

	if( SetupLSM() )
	{
		uart0_sendStr("Retry LSM\r\n");
		goto retryi2c;
	}


	if( SetupAVRTool() )
	{
		uart0_sendStr("Retry AVRTool\r\n");
		goto retryi2c;		
	}



	if( SetupBMP085() )
	{
		uart0_sendStr("Retry BMP\r\n");
		goto retryi2c;
	}
skip_i2c:

	//Add a process
	system_os_task(procTask, procTaskPrio, procTaskQueue, procTaskQueueLen);

	uart0_sendStr("\r\nCustom Server\r\n");
	uart0_sendStr("NewTest5\r\n");

	ControlInit();
	//Timer example
	os_timer_disarm(&some_timer);
	os_timer_setfn(&some_timer, (os_timer_func_t *)MyTimer, NULL);
	os_timer_arm(&some_timer, 10, 1); // was 6, 166.66 Hz update rate... let's try 100hz


	system_os_post(procTaskPrio, 0, 0 );
}

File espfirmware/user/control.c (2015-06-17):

#include "control.h"
#include "ets_sys.h"
#include "os_type.h"
#include "mem.h"
#include "spi_flash.h"
#include "lsm9ds1.h"
#include "bmp085.h"
#include "osapi.h"
#include "mem.h"
#include "c_types.h"
#include "user_interface.h"
#include "ets_sys.h"
#include "driver/uart.h"
#include "espconn.h"
#include "http.h"
#include "flash_rewriter.h"

extern SpiFlashChip * flashchip;
struct espconn *pespconn;

//GYR X, GYR Y, GYR Z
//ACC X, ACC Y, ACC Z
//MAG X, MAG Y, MAG Z
//MTEMP, BTEMP, BAROMETER

uint32_t pressure;
uint16_t bmptemp;
uint32_t systemFrame;

int in_range_setting;
int stream_data = 0;
int stream_data_raw = 0;

int32_t  gyrNow[3];
int32_t	 accNow[3];
int32_t  magNow[3];
int32_t  barNow;
int32_t  tempNow;  //tenths of degrees 
int16_t  targetAxes[4]; //Expected -10,000..10,000 (L/R, FWD/BKD, Orient, elevator)

int		  voltNow;
uint8_t  gMotors[4];
uint8_t  motors_automatic = 0; //whether in flight? Maybe?
uint8_t timeout_for_ma = 0;
//Used only for centering.
int32_t  gyrIIR[3];
int32_t  accIIR[3];
int32_t  magIIR[3];
int32_t  barIIR;


uint32_t calgyro[3];
uint32_t calacc[3];
uint32_t calmag[3];

int16_t sensordata[10];
int8_t  sensorstatus;
int8_t sensor_data_valid;

int bus_online = 1;

struct SaveSector settings;










///////////////////////////////////////////////////////////////////////////////////////
/////////////////// This awful code is my stand-in for a control loop.
/////////////////// I REALLY HOPE it gets 100% trashed!
struct Pid
{
	int32_t error;
	int32_t last;
	int32_t i;
	int32_t d;

	int32_t kp; //unity = 256
	int32_t ki; //unity = 256
	int32_t kd; //unity = 256
	int32_t outmax; //Should be 12800

	int32_t output;
} PIDs[3];

void RunPid( struct Pid * p )
{
	p->d = p->error - p->last;
	p->i += p->error;

	int32_t ci = ((p->i * p->ki)>>(8+GYRIIRDEP));

	if( ci > p->outmax )
	{
		p->i = (p->outmax / p->ki)<<(8+GYRIIRDEP);
	}
	else if( ci < -p->outmax )
	{
		p->i = -((p->outmax / p->ki)<<(8+GYRIIRDEP));

	}

	p->output = ((p->error * p->kp) + (p->i * p->ki) + (p->d * p->kd))>>(8+GYRIIRDEP);

	if( p->output > p->outmax )
	{
		p->output = p->outmax;
	}
	else if( p->output < -p->outmax )
	{
		p->output = -p->outmax;
	}
}


void HandleClosedLoopMotors()
{
	int i;
	char buffer[128];
	static int32_t iir_spin;
	static int32_t iir_leftright;
	static int32_t iir_fwdbak;

	if( timeout_for_ma++ > 30 )
	{
		motors_automatic = 0;
	}

	int32_t in_spin = ((int32_t)(calgyro[2]));  //POSITIVE = moving counter-clockwise.
//	int32_t in_leftright = ((int32_t)(calacc[1])); //LEFT = POSITIVE, RIGHT = NEGATIVE
//	int32_t in_fwdbak = ((int32_t)(calacc[0]));    //FWD = NEGATIVE, REVERSE = POSITIVE
	int32_t in_leftright = -((int32_t)(calgyro[0])); //LEFT = POSITIVE, RIGHT = NEGATIVE
	int32_t in_fwdbak = ((int32_t)(calgyro[1]));    //FWD = NEGATIVE, REVERSE = POSITIVE


#define IIRA 0
#define MOTIONMUX 100

/*	iir_spin = (iir_spin + in_spin) - (iir_spin>>IIRA);
	iir_leftright = (iir_leftright + in_leftright) - (iir_leftright>>IIRA);
	iir_fwdbak = (iir_fwdbak + in_fwdbak) - (iir_fwdbak>>IIRA);

	int32_t spin = iir_spin >> IIRA;
	int32_t leftright = iir_leftright >> IIRA;
	int32_t fwdbak = iir_fwdbak >> IIRA;
*/

	int32_t spin = in_spin;
	int32_t leftright = in_leftright;
	int32_t fwdbak = in_fwdbak;

	PIDs[0].error = spin + targetAxes[2]>>2;
	PIDs[1].error = leftright + targetAxes[0]>>2;
	PIDs[2].error = fwdbak - targetAxes[1]>>2;

	RunPid( &PIDs[0] );
	RunPid( &PIDs[1] );
	RunPid( &PIDs[2] );



	spin = PIDs[0].output;
	leftright = PIDs[1].output;
	fwdbak = PIDs[2].output;

	//Joystick foward = negative
	//Joystick right = positive.

//	leftright += targetAxes[0]; //Positve = move right
//	fwdbak -= targetAxes[1];   //Positive = 
//	spin -= targetAxes[2];

/*	spin = (spin * 310)>>8;
	leftright = (leftright * 350)>>8;
	fwdbak  = (fwdbak*350)>>8;*/

	//M0: Front, right, clockwise
	//M1: Rear, right, counter-clockwise
	//M2: Rear, left, clockwise
	//M3: Front, left, counter-clockwise

	int m1 = -leftright - fwdbak - spin;
	int m2 = -leftright + fwdbak + spin;
	int m3 =  leftright + fwdbak - spin;
	int m4 =  leftright - fwdbak + spin;

	ets_sprintf( buffer, "MD\t%d\t%d\t%d\t%d\n", m1, m2, m3, m4 );
	if( pespconn )
		espconn_sent( pespconn, buffer, ets_strlen( buffer ) );

	m1 = (m1 + (targetAxes[3]))>>6;
	m2 = (m2 + (targetAxes[3]))>>6;
	m3 = (m3 + (targetAxes[3]))>>6;
	m4 = (m4 + (targetAxes[3]))>>6;

	if( m1 < 0 ) m1 = 0;
	if( m2 < 0 ) m2 = 0;
	if( m3 < 0 ) m3 = 0;
	if( m4 < 0 ) m4 = 0;

	if( m1 > 255 ) m1 = 255;
	if( m2 > 255 ) m2 = 255;
	if( m3 > 255 ) m3 = 255;
	if( m4 > 255 ) m4 = 255;

const uint8_t ThrustCurve[] = {
          0,  28,  32,  36,  39,  42,  44,  47,  49,  51,  53,  55,  57,  59,  61,  63, 
         64,  66,  67,  69,  71,  72,  74,  75,  77,  78,  79,  81,  82,  83,  85,  86, 
         87,  89,  90,  91,  92,  93,  95,  96,  97,  98,  99, 100, 102, 103, 104, 105, 
        106, 107, 108, 109, 110, 111, 112, 113, 114, 115, 116, 117, 118, 119, 120, 121, 
        122, 123, 124, 125, 126, 127, 128, 129, 130, 131, 132, 132, 133, 134, 135, 136, 
        137, 138, 139, 140, 140, 141, 142, 143, 144, 145, 146, 146, 147, 148, 149, 150, 
        151, 151, 152, 153, 154, 155, 155, 156, 157, 158, 159, 159, 160, 161, 162, 162, 
        163, 164, 165, 166, 166, 167, 168, 169, 169, 170, 171, 172, 172, 173, 174, 174, 
        175, 176, 177, 177, 178, 179, 180, 180, 181, 182, 182, 183, 184, 185, 185, 186, 
        187, 187, 188, 189, 189, 190, 191, 191, 192, 193, 193, 194, 195, 195, 196, 197, 
        198, 198, 199, 200, 200, 201, 201, 202, 203, 203, 204, 205, 205, 206, 207, 207, 
        208, 209, 209, 210, 211, 211, 212, 212, 213, 214, 214, 215, 216, 216, 217, 217, 
        218, 219, 219, 220, 221, 221, 222, 222, 223, 224, 224, 225, 225, 226, 227, 227, 
        228, 228, 229, 230, 230, 231, 231, 232, 233, 233, 234, 234, 235, 236, 236, 237, 
        237, 238, 238, 239, 240, 240, 241, 241, 242, 243, 243, 244, 244, 245, 245, 246, 
        247, 247, 248, 248, 249, 249, 250, 250, 251, 252, 252, 253, 253, 254, 254, 255, };


	gMotors[0] = ThrustCurve[m1];
	gMotors[1] = ThrustCurve[m2];
	gMotors[2] = ThrustCurve[m3];
	gMotors[3] = ThrustCurve[m4];


	for( i = 0; i < 4; i++ )
	{
		if( targetAxes[i] > 0 ) targetAxes[i]--;
		else targetAxes[i]++;
	}
}
/////////////////// This awful code is my stand-in for a control loop.
/////////////////// I REALLY HOPE it gets 100% trashed!
///////////////////////////////////////////////////////////////////////////////////////














void ICACHE_FLASH_ATTR ResetIIR()
{
	int i;
	for( i = 0; i < 3; i++ )
		gyrIIR[i] = gyrNow[i]<<GYRIIRDEP;
	for( i = 0; i < 3; i++ )
		accIIR[i] = accNow[i]<<ACCIIRDEP;
	for( i = 0; i < 3; i++ )
		magIIR[i] = magNow[i]<<MAGIIRDEP;
	barIIR = barNow<<BARIIRDEP;
}
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

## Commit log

2015-06-09 Initial commit from private repository to github.
    As a warning, a lot of this is barely tested and there are some minor, untested hardware changes, too.
    [wiflier.kicad_pcb, wiflier.sch]
2015-06-09 update rather embarrasing compiler error
    [control.c]
2015-06-09 fix up the commands some
    [control.c]
2015-06-10 total rework over a lot of stuff, now we have sort of closed loop control.
    [wiflier.sch]
2015-06-11 Fix I2c timing some, avoid float's.
    [control.c, i2c.c, lsm9ds1.c]
2015-06-12 update to rev A
    [wiflierA.kicad_pcb, wiflierA.sch]
2015-06-13 update with correct i2c timing, better interpretation, and closing in on a control loop
    [control.c, i2c.c]
2015-06-13 Update with driver for hand-held controllers
    [wiflierA.kicad_pcb, wiflierA.sch]
2015-06-13 Almost... now I'm getting faults on the IMU, and no idea why.
2015-06-15 switch switching frequency up a lot.
    Seems to solve most problems.
    [control.c, test.c, user_main.c]
2015-06-17 fix scanplace so it doesn't accumulate entries.
    [control.c]
2015-06-23 Add wifiler A and B.
    [wiflierA-B_Cu.gbl, wiflierA-B_Mask.gbs, wiflierA-B_SilkS.gbo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]
2015-06-23 remove wiflier A, keep B
    [wiflierA-B_Cu.gbl, wiflierA-B_Mask.gbs, wiflierA-B_SilkS.gbo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]
2015-08-13 Woah, too many commits to count. I guess I just havne't committed anything here in a looong time.
    [wiflierB-B_Cu.gbl, wiflierB-B_Mask.gbs, wiflierB-B_SilkS.gbo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]
2015-08-13 add new wiflier stuff
    [wiflier_EXP_B.kicad_pcb, wiflier_EXP_B.sch]
2015-08-28 General updates with MPFS thing
    [wiflier_EXP_B.kicad_pcb, wiflier_EXP_B.sch]
2016-09-10 Add an initial stab at this new wiflier.
    [wiflier8285.kicad_pcb, wiflier8285.sch]
2016-09-14 tweaks to output stuff
    [wiflier8285.kicad_pcb]
2016-10-30 add 8285 version of wiflier.
    [wiflier8285-B.Cu.gbl, wiflier8285-B.Mask.gbs, wiflier8285-B.SilkS.gbo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]

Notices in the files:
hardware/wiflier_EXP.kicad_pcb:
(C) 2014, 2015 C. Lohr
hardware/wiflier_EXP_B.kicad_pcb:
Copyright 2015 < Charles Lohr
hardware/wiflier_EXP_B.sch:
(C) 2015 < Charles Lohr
